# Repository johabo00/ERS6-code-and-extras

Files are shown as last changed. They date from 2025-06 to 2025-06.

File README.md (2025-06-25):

The Computer and Robot contains the files created for integration of ROS 2, running on the computer and robot respectivly
Microcontroller code is the code running on the upper ESP32 while ROS 2 is running
Hardware demo is the code running on the ESP32 without ROS 2 (described in Chapter 11)
STEPfiles contains all the custom mechanical components made for the robot.

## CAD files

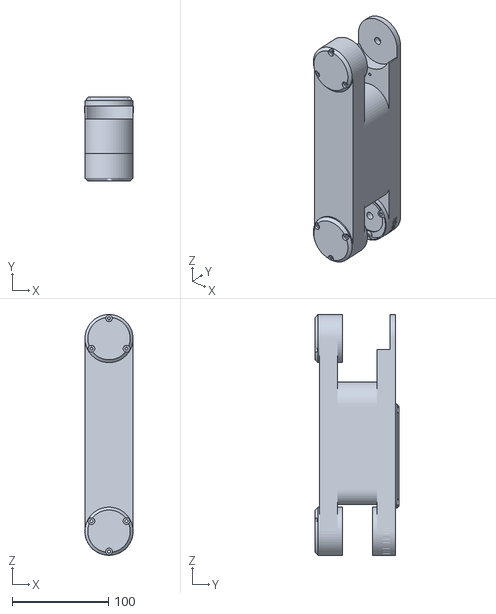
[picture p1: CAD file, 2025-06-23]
Computer/src/ers6_description/meshes/a4.stl
50.4 x 87.0 x 250.2

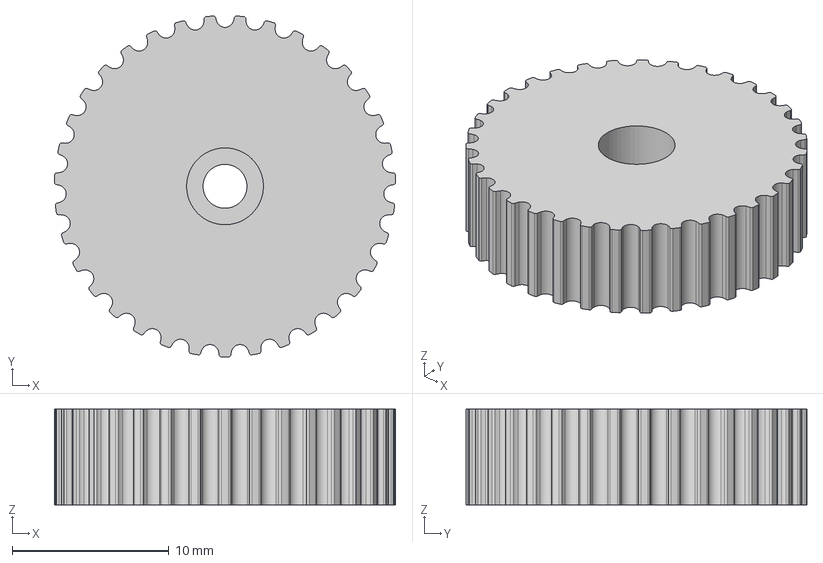
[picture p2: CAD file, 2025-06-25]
STEPfiles/P204.step
21.8 x 21.7 x 6.10 mm

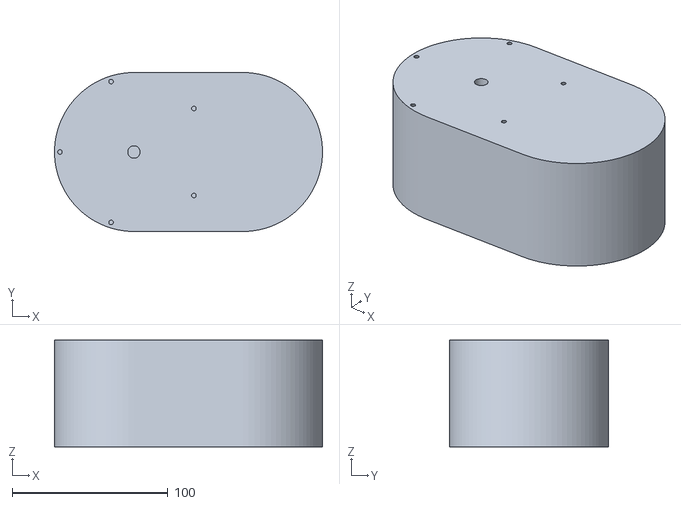
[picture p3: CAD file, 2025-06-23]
Computer/src/ers6_description/meshes/Base.stl
172.0 x 102.0 x 68.4

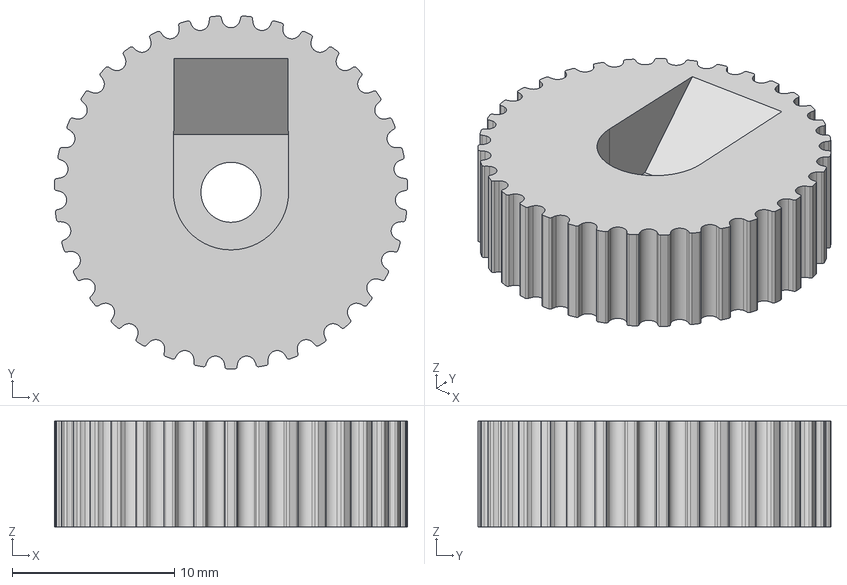
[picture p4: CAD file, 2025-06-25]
STEPfiles/P103.step
21.8 x 21.7 x 6.50 mm

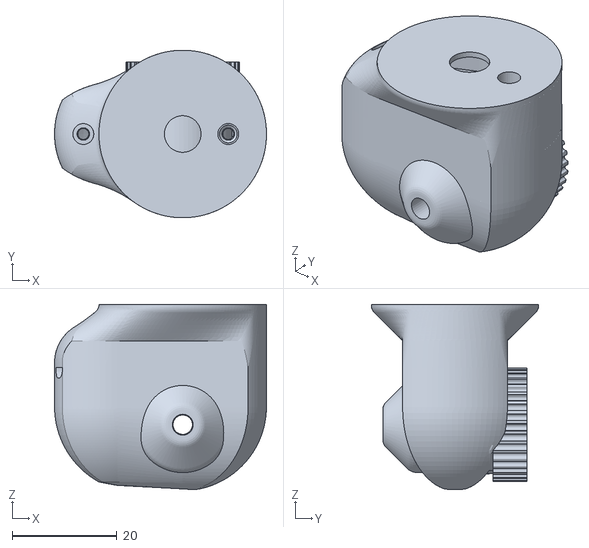
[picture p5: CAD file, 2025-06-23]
Computer/src/ers6_description/meshes/a1.stl
40.5 x 32.0 x 35.4

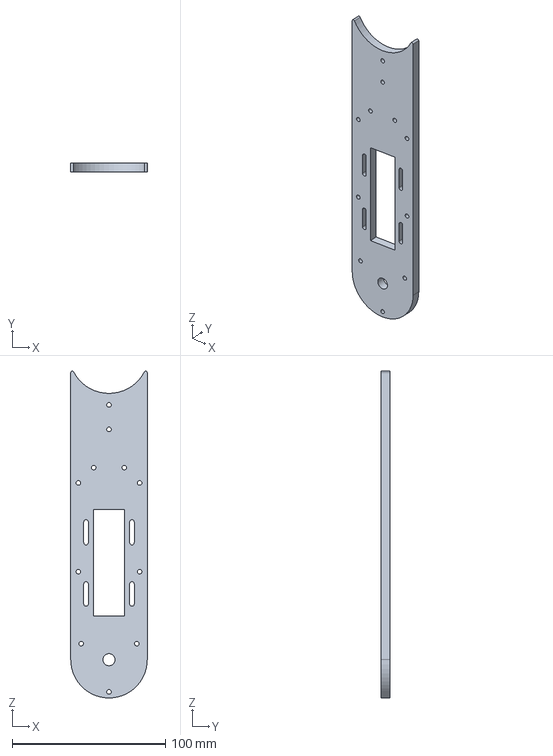
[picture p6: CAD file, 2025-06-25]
STEPfiles/W404.step
50.0 x 6.00 x 213.6 mm

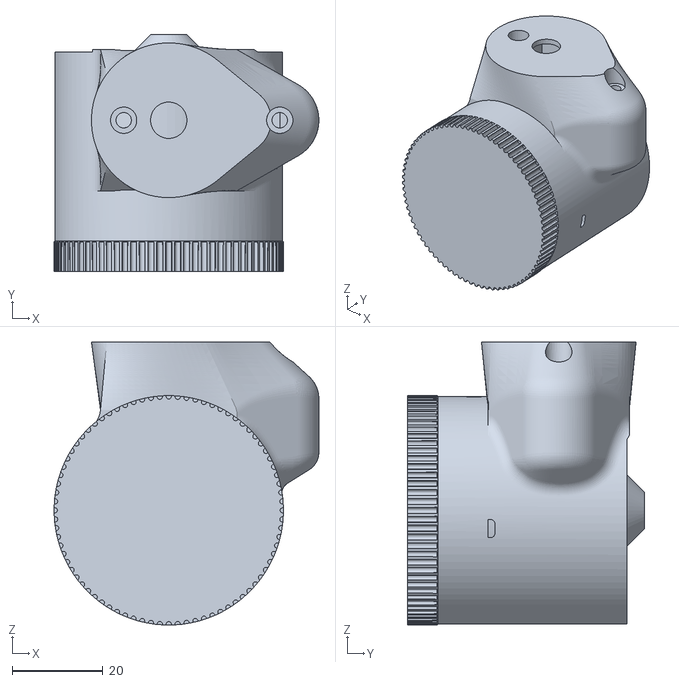
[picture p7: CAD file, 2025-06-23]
Computer/src/ers6_description/meshes/a3.stl
58.2 x 52.1 x 62.2

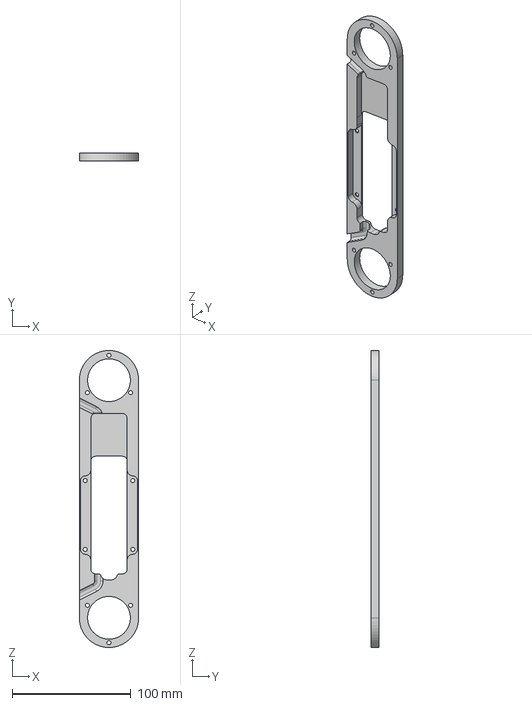
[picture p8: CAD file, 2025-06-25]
STEPfiles/P401.step
50.0 x 7.00 x 250.0 mm

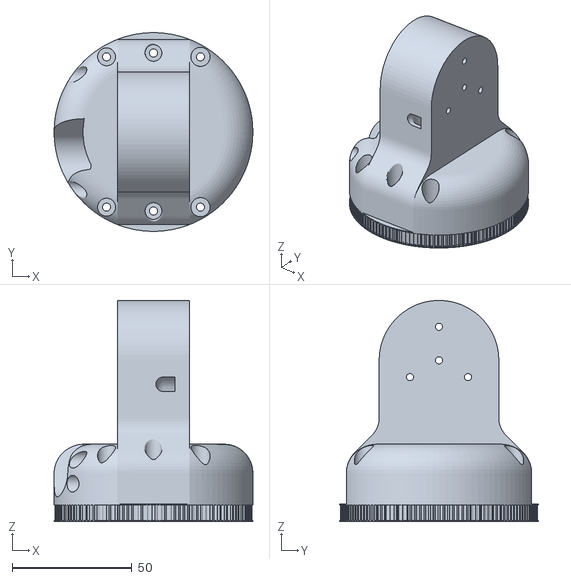
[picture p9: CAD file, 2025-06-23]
Computer/src/ers6_description/meshes/a5.stl
83.0 x 83.0 x 92.3

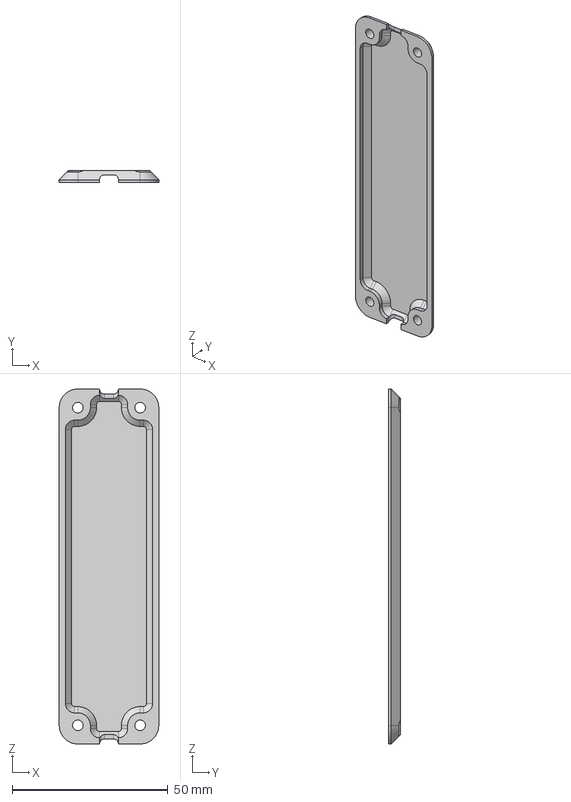
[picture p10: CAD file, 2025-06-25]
STEPfiles/P206.step
32.0 x 3.90 x 114.0 mm

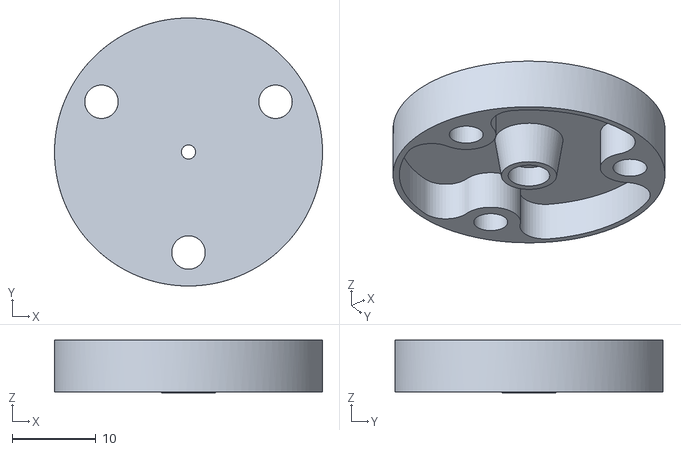
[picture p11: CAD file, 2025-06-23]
Computer/src/ers6_description/meshes/a0.stl
32.0 x 32.0 x 6.30

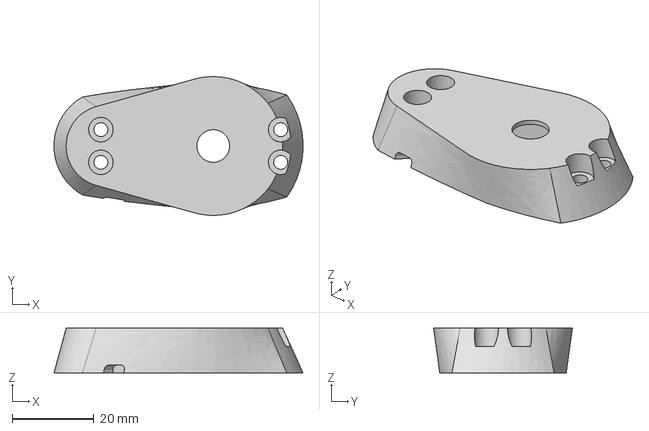
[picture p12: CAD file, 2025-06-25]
STEPfiles/P302.step
60.9 x 34.0 x 11.0 mm

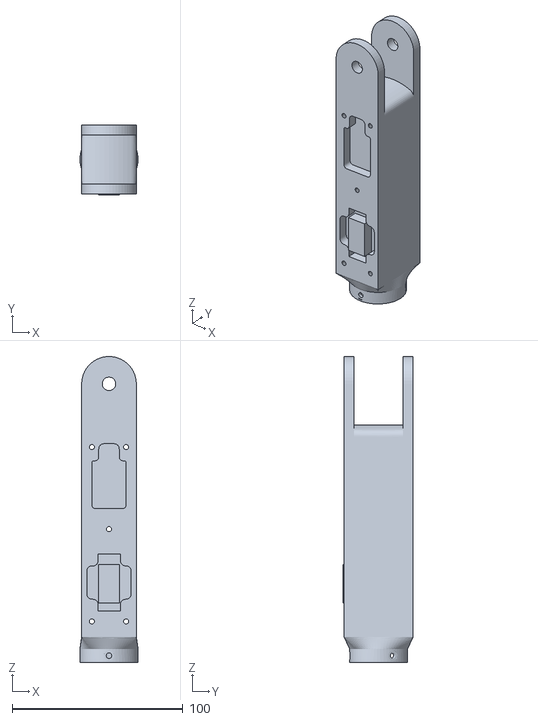
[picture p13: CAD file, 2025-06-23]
Computer/src/ers6_description/meshes/a2.stl
34.0 x 41.2 x 179.0

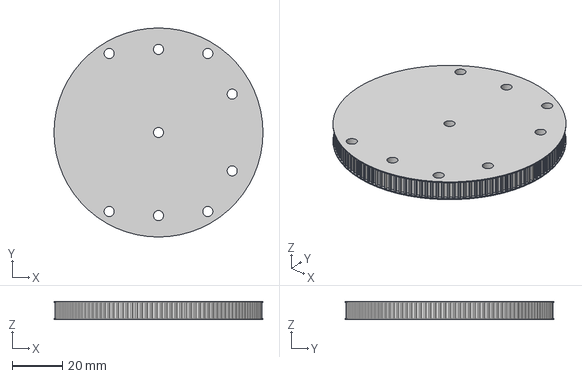
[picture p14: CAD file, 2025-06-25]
STEPfiles/P502.step
83.0 x 83.0 x 7.30 mm

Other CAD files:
STEPfiles/P102.step
STEPfiles/P205.step
STEPfiles/P506.step
STEPfiles/W603.step
STEPfiles/P101.step
STEPfiles/P104.step
STEPfiles/P201.step
STEPfiles/P202.step
STEPfiles/P203.step
STEPfiles/P301.step
STEPfiles/P303.step
STEPfiles/P304.step
STEPfiles/P402.step
STEPfiles/P403.step
STEPfiles/P404.step
STEPfiles/P405.step
STEPfiles/P406.step
STEPfiles/P407.step
STEPfiles/P408.step
STEPfiles/P409.step
STEPfiles/P410.step
STEPfiles/P411.step
STEPfiles/P501.step
STEPfiles/P503.step
STEPfiles/P504.step
STEPfiles/P507.step
STEPfiles/P601.step
STEPfiles/P602.step
STEPfiles/P603.step
STEPfiles/P606.step
STEPfiles/W201.step
STEPfiles/W202.step
STEPfiles/W401.step
STEPfiles/W402.step
STEPfiles/W403.step
STEPfiles/W501.step
STEPfiles/W502.step
STEPfiles/W601.step
STEPfiles/W602.step
STEPfiles/magholder.step

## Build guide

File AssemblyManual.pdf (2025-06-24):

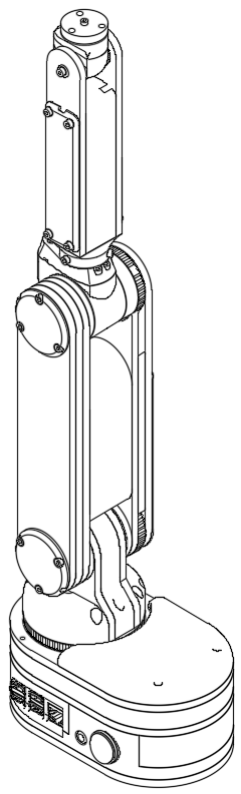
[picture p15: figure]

Assembly Manual
Version 1.0
18.06.2025

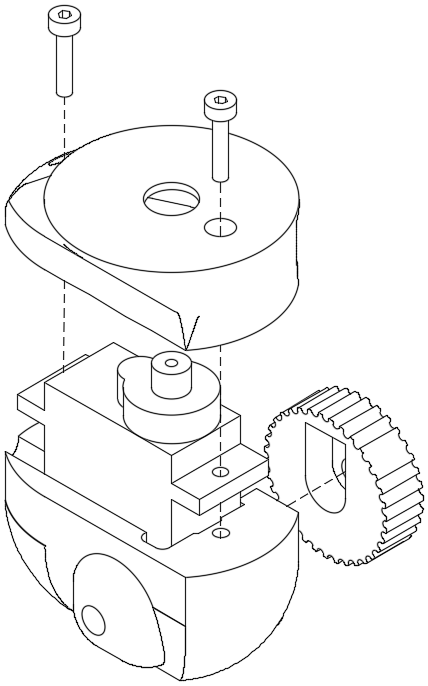
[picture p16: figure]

Assembly 1: Step 1
- Custom: P101, P102, P103
- Ordered: MG90S
- Bolts: M2x10mm [x2]
- Fasten the servo motor between P101 and P102 (screws directly into the plastic)
- Motor wires are channeled out an opening in the back P103 sits loose on P101

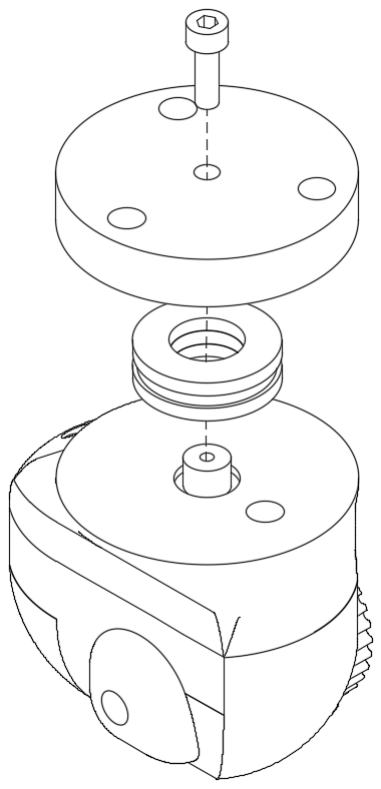
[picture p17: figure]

Assembly 1: Step 2
- Custom: P104
- Ordered: Thrust bearing (16x8x5)
- Bolts: M2.5x8mm
- Fasten P104 to the servo shaft, separated by the thrust bearing. Use thread-lock glue

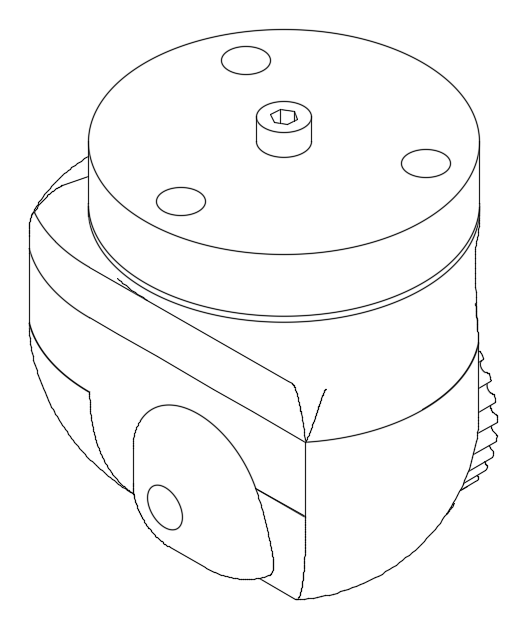
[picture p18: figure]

Assembly 2: Step 1
- Custom: P203, P204
- Ordered: MG90S
- Bolts: M2x8mm [x2], M2.5x5mm [x1]
- Fastenthe servomotor to P203 with the M2 bolts.
- Fasten P204 to the servo-shaft with a M2.5 bolt, use threadlock glue.

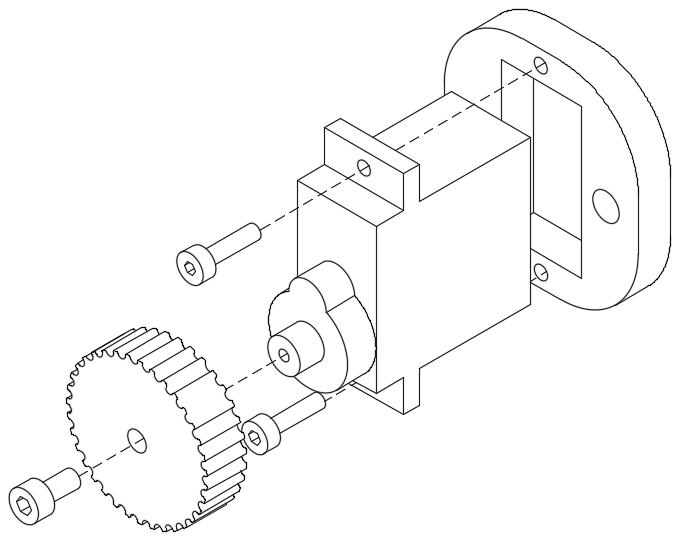
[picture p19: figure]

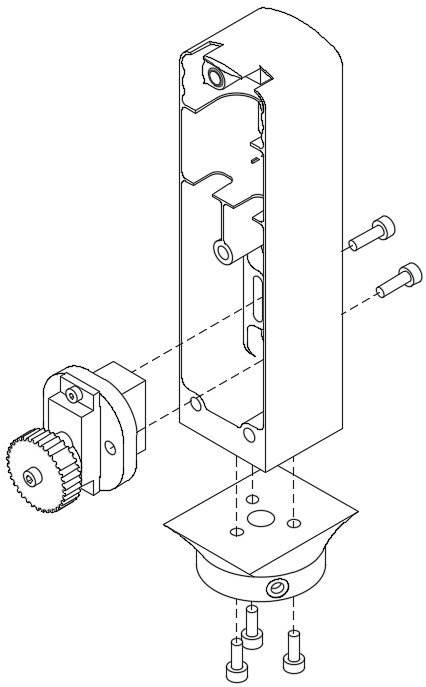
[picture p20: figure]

Assembly 2: Step 2
- Custom: P201, P202
- Bolts: M3x8mm [x3], M3x10mm [x2]
- Fasten P201 and P202 with three M3x8
- Connect the motor assembly to the slots so it can move up and down

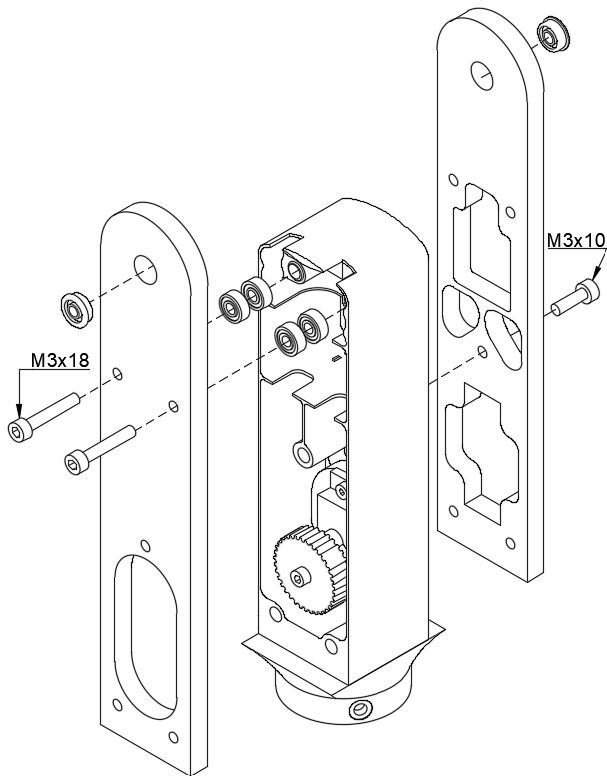
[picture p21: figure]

Assembly 2: Step 3
- Custom: W201, W202
- Ordered: MR83ZZ [x4], MF83ZZ [x2], GT2 Timing belt
- Bolts: M3x10mm [x1], M3x18mm [x2]
- Position the timing belt around P204 and between the MR83ZZ bearings
- Fasten W202 to P201 with two M3x18 bolts. NB: they go through the bearings placed above
- W201 is connected by a single M3x10
- Press the MF83ZZ into place

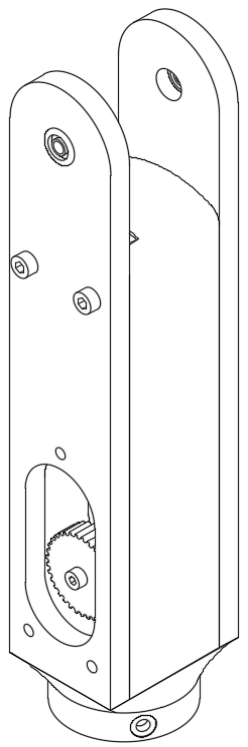
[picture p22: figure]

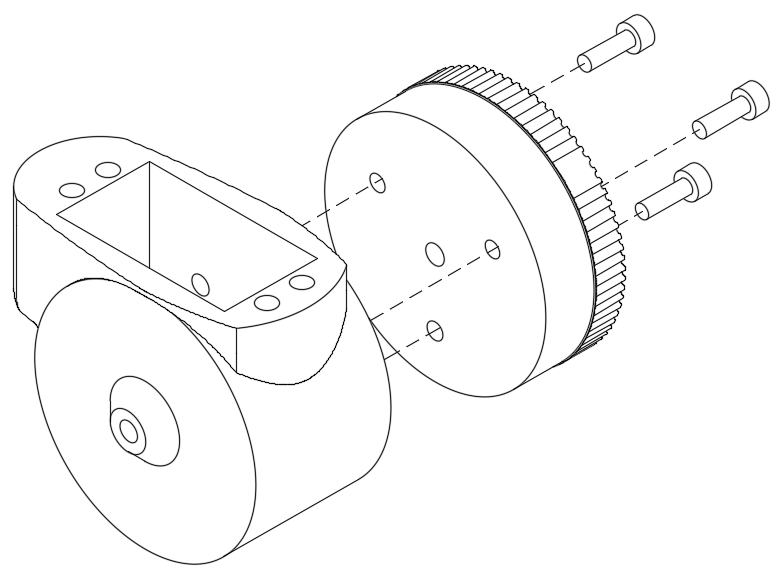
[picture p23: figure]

Assembly 3: Step 1
- Custom: P301, P303
- Bolts: M3x10 [x3]
- Connect P301 and P302 with three M3x10 bolts

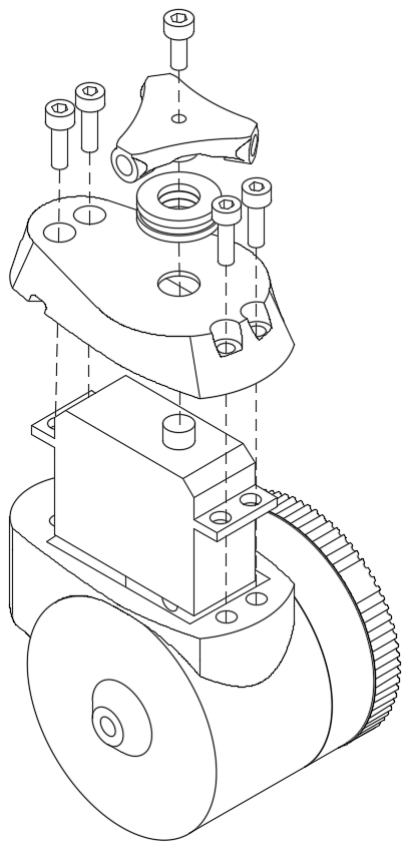
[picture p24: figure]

Assembly 3: Step 2
- Custom: P302, P304
- Ordered: TD-9225MG, Thrust bearing (16x8x5)
- Bolts: M3x8 [x1], M3x10 [x4]
- Mount the servo motor in between P301 and P302 with four M3x10 bolts. Motor cables are led out a channel in the back
- Fasten P304 to the servo shaft with a M3x8 with a thrust-bearing in between. Use threadlock glue

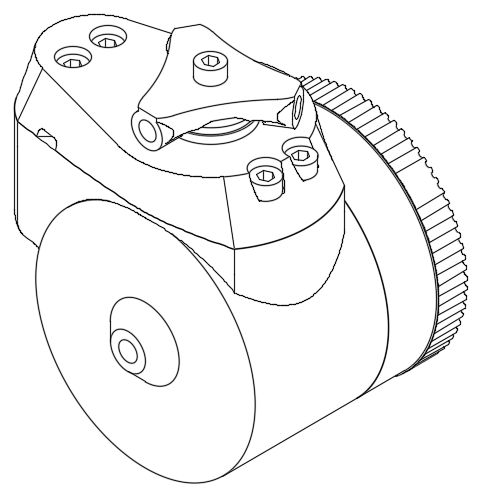
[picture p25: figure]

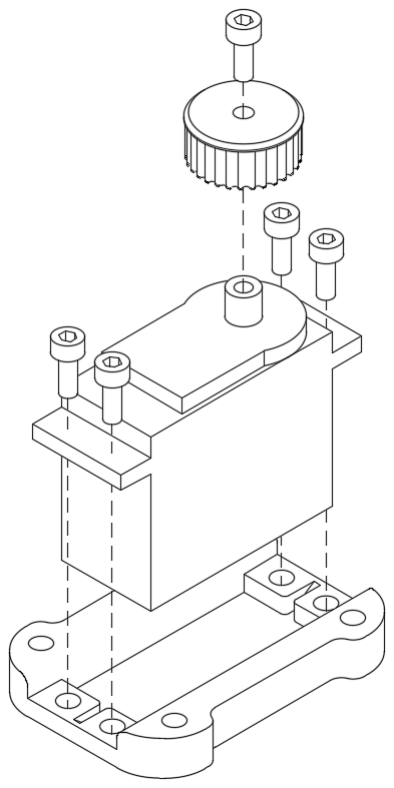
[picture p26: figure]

Assembly 4: Step 1
- Custom: P406, P410
- Ordered: MG996R
- Bolts: M3x8 [x5]
- Mount the servo motor to P406 with four bolts
- Fasten P410 to the servo shaft with a M3x8. Use threadlock glue

Assembly 4: Step 2
- Custom: P404, P407, P408, W404
- Bolts: M3x10 [x4], M3x12 [x5]

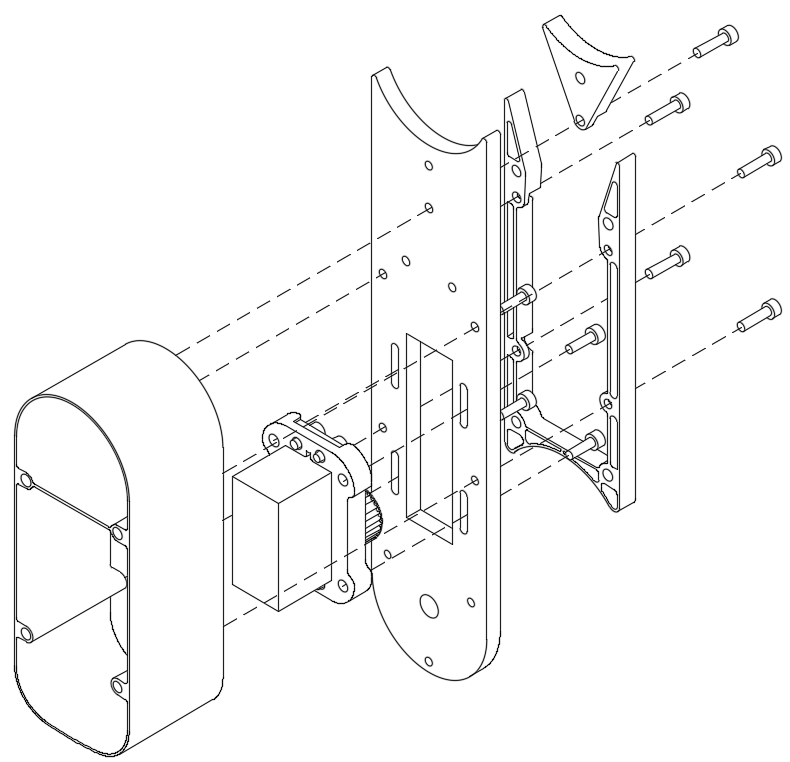
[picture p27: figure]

- Mount the motor assembly to W404
- Fasten P404, P407 and P408 with 5 M3x12

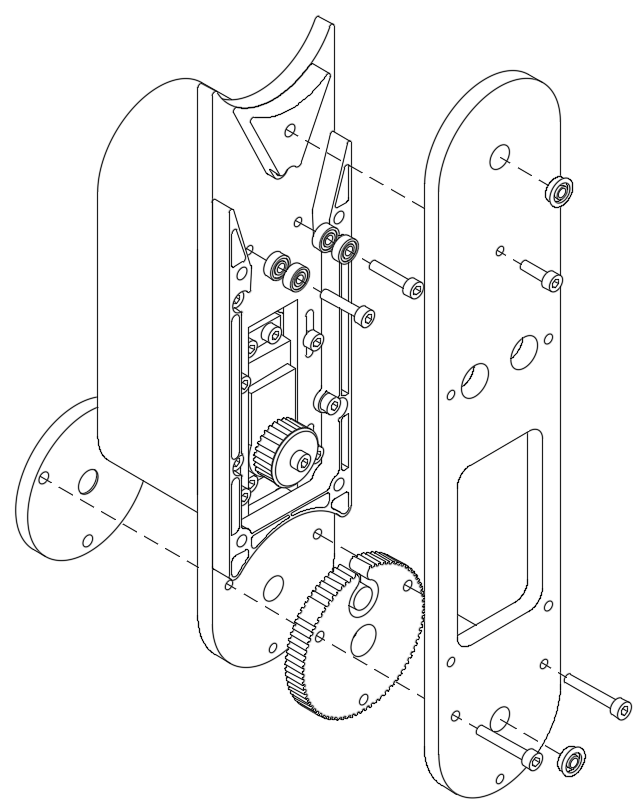
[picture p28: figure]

Assembly 4: Step 3
- Custom: P403, P409, W403
- Ordered: MR83ZZ [x4], MF83ZZ [x2], GT2 Timing belt, GT2 Timing belt
- Bolts: M3x10 [x1], M3x15 [x2], M3x22 [x2]
- Fasten the MR83ZZ with
M3x15
- Place the timing belts in position
- Fasten W403, P403 and P409. NB a ziptie can be used
around the belt in the gap
- Press in the MF83ZZ. The lower goes to W404

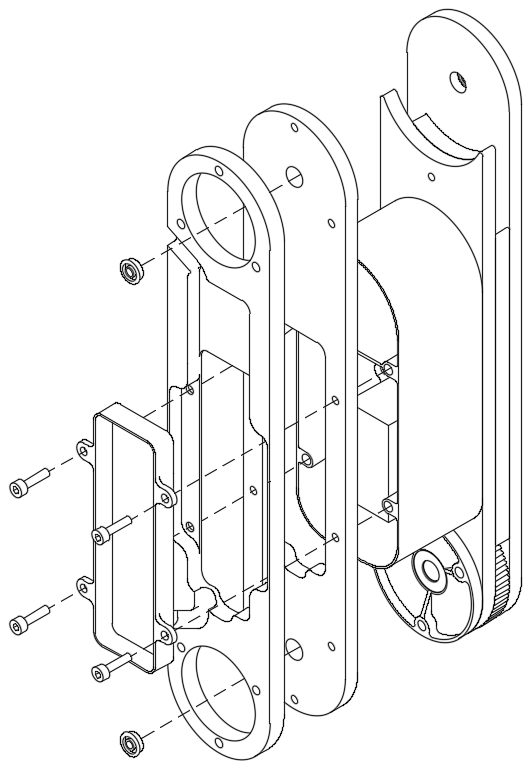
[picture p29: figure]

Assembly 4: Step 4
- Custom: P401, P402, W401
- Ordered: MF83ZZ [x2]
- Bolts: M3x12 [x4]
- Fasten P401, P402 and W401 to P404 with M3x12
- The motor cables are routed out underneeth P402
- Press in the MF83ZZ

Assembly 5: Step 1
- Custom: P501, P502, W502
- Bolts: M3x10 [x4]
- Fasten P501 and P502
- Fasten W502 to P501

Assembly 5: Step 2
- Custom: P503, P505, W501
- Ordered: MG996R
- Bolts: M3x8 [x1], M3x25 [x4]

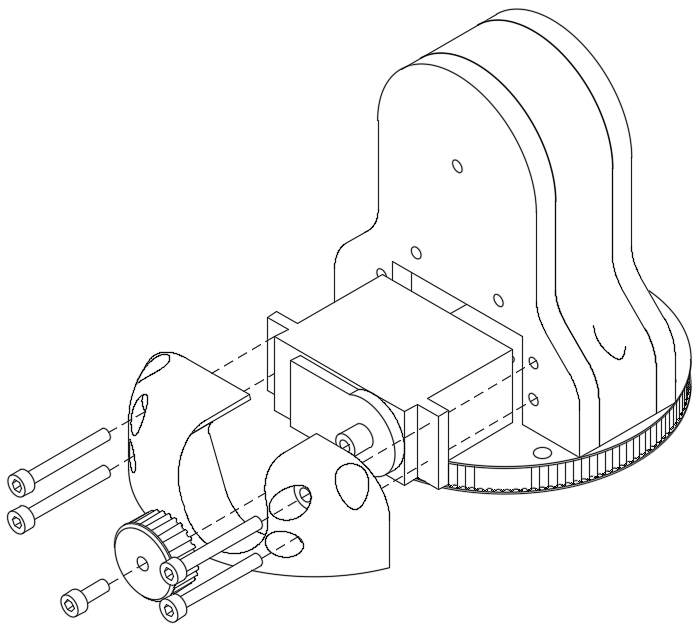
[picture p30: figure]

- Mount the servo, W501 and P503 to P501 with 4 M3x25
- Fasten P505 to the servo shaft with a M3x8, use threadlock glue

Assembly 5: Step 3
- Custom: P506, P507
- Ordered: MR83ZZ [x4]
- Bolts: M3x10 [x3], M3x15 [x1], M3x25 [x1]

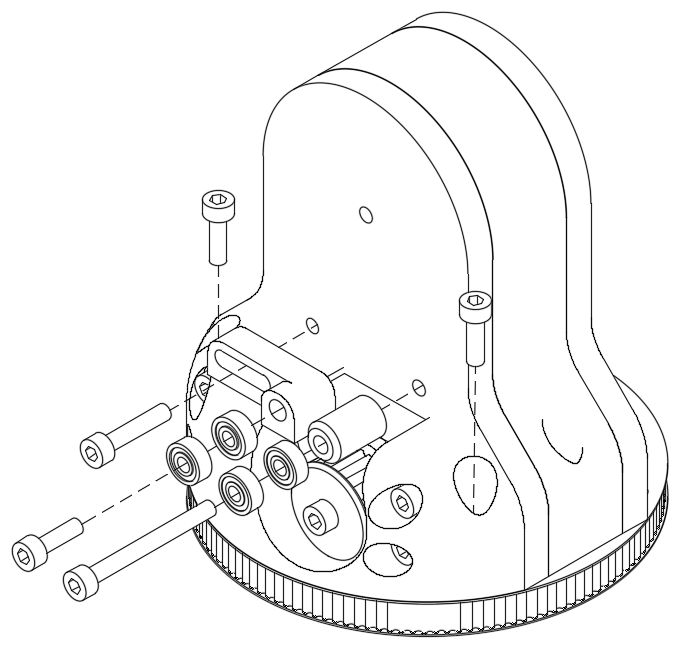
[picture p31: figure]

- Fasten P503 to P502 with two M3x10
- Mount P506 to W501/P501
with M3x15
- Fasten 2 bearings in P506 with a M3x10
- Fasten 2 bearings through P507 to P501 with a M3x25

Assembly 6: Step 1
- Custom: P601
- Ordered: DC/DC Converter, Switch, Barrel Jack, Raspberry Pi
- Press the Raspberry into position in P601
- Fit the barrel jack and switch
- Place the DC/DC converter
- Make the connections
between switch, jack and
converter

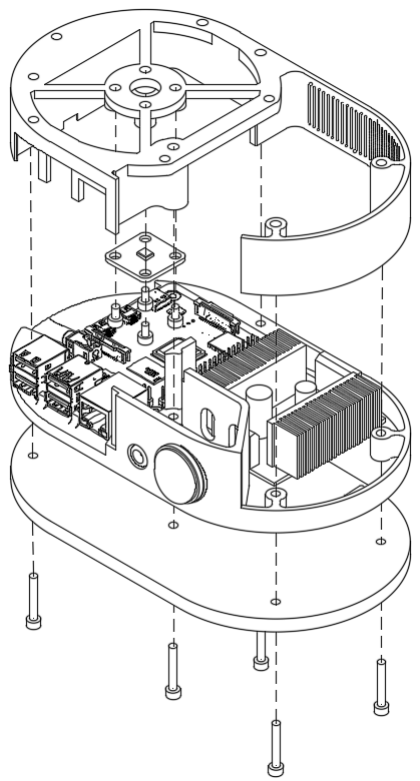
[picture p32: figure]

Assembly 6: Step 2
- Custom: P602, W601
- Ordered: AS5600
- Bolts: M3x5 [x4], M3x20 [x5]
- Fasten the AS5600 with 4 M3x5
- Fit P602 to P601
- Fasten W601 with 5 M3x20

Assembly 6: Step 3
- Custom: P604, P605, W603
- Ordered: MG996R
- Bolts: M3x8 [x5], M3x10 [x4]
- Mount the servo motor to P604 with 4 M3x8
- Fasten P605 to the servo shaft with a M3x8. Use threadlock glue
- Fasten P604 to W601 with 4 M3x10

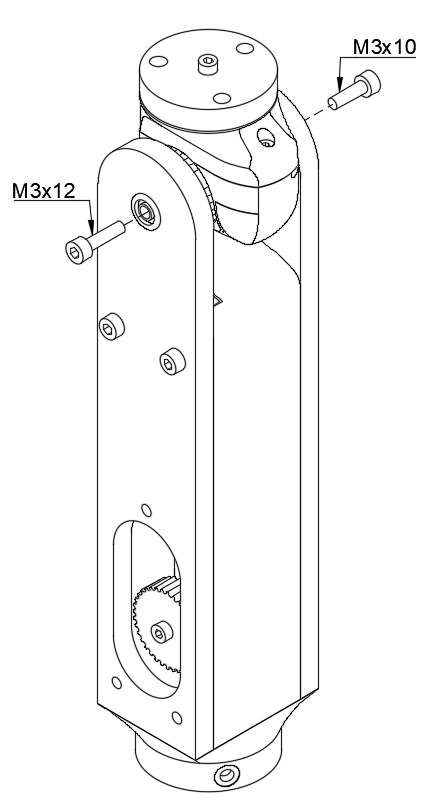
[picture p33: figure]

General assembly: Step 1
- Assemblies: A1, A2
- Bolts: M3x10 [x1], M3x12 [x1]
- Fit the A1 in A2, make sure the timing belt goes around A1 pulley
- Fasten with bolts, use
threadlock glue. NB: not tight, ensure free rotation

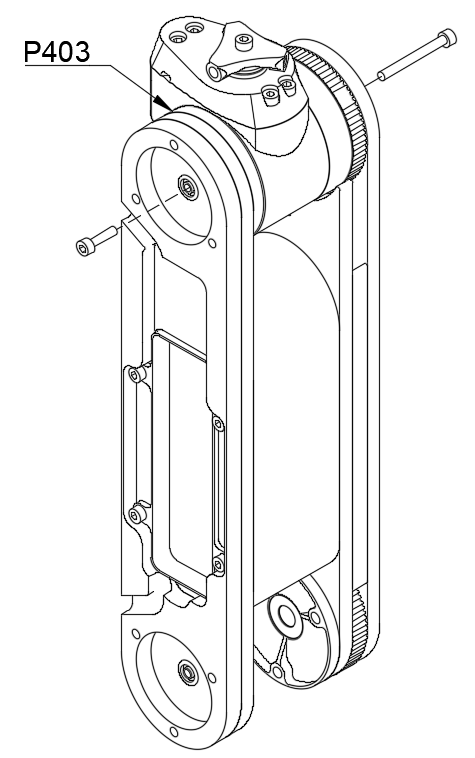
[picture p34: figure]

General assembly: Step 2
- Assemblies: A3, A4
- Components: P403
- Bolts: M3x12 [x1], M3x30 [x1], M3 standoff (5mm)
- Place P403 in position, this will be fastened later
- Fasten the M3x12 to the
standoff, through the bearing (cable side)
- Fasten A3 to the two bolts, use threadlock glue
- The belt can be tensioned

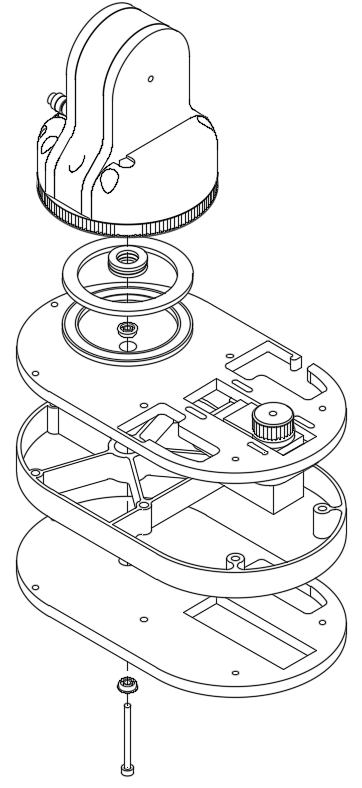
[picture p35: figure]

General assembly: Step 3
- Assemblies: A5
- Components: P603, W602,
W603, Thrust-bearing duct
- Ordered: MF83ZZ [x2], Thrust bearing(18x10x5.5), 4.5mm steel balls
- Bolts: M3x35 [x1]
- Fill the printed thrust bearing with metal balls, use
lubrication
- Press MF83ZZ to W602 and W603
- Fasten A5 to the A6 assembly with a M3x35

General assembly: Step 4
- Assemblies: A5, A6
- Components: Magnetholder
- Bolts: M3x35 [x5]
- Pressfit the magnetholder with magnet to the M3x35
connecting A5 to A6
- Connect with 5 M3x35

General assembly: Step 5
- Assemblies: A1-A4
- Bolts: M3x5 [x3]
- Connect A2 to A3 with 3 M3x5

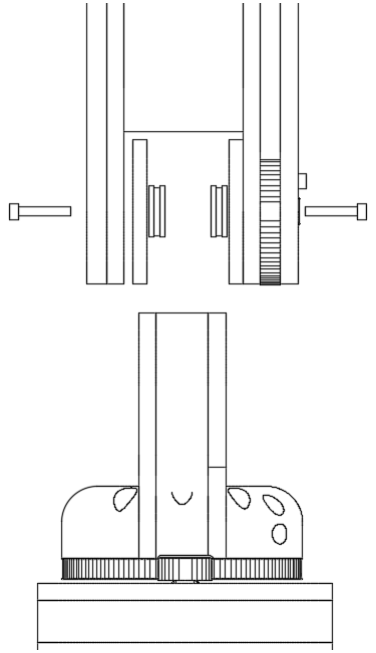
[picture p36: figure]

General assembly: Step 6
- Assemblies: All
- Components: P403
- Ordered: Thrust bearing
(18x10x5.5)
- Bolts: M3x18 [x2]
- Place P403 and bearings
- Slide onto A5 and fasten with bolts

Cabeling
- Ordered: ESP32-C3 supermini [x2], wires, I2C multiplexer
- Bolts: M3x5 [x4]
- Use the schematics figure from chapter 9
- One ESP32 is going in A2, the other in A6
- The power cables are connected in DC/DC-converter for A6, two M3x5 and inserts in A5 and A2
- I2C lines are connected with JST connectors
- I2C on AS5600 goes through the I2C multiplexer
(NB: Cables are soldered directly to board)
- It is recommended to use cable-sleeves in A6-A5, A5-A4 and A4-A3
- Set 5v output on converter
(wago-terminals can be used in A4)

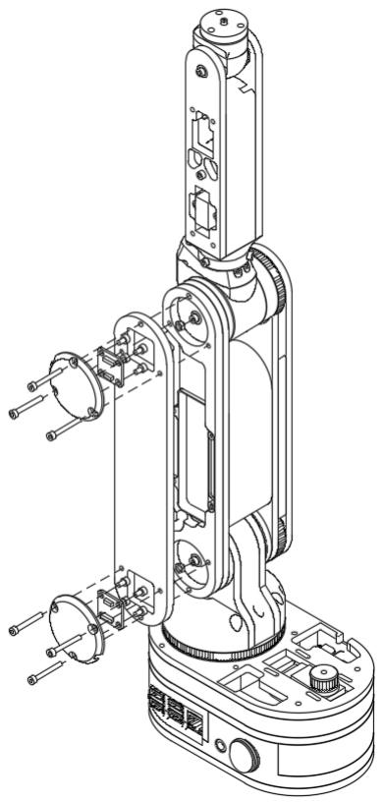
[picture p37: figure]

Cover assembly: Step 1
- Components: P405 [x2],
W402, Magnetholder [x2]
- Ordered: AS5600 [x2]
- Bolts: M3x5 [x8], M3x25 [x25]
- Fit magnetholders w. magnets to bolts in joints
- Fasten the encoders to P405 with M3x5
- Fit all wires in cable gate in A4 and place W402 over
- Fasten P405 to A4 with M3x25

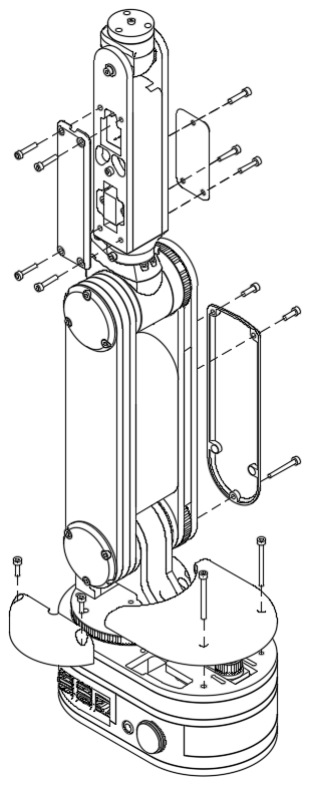
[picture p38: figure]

Cover assembly: Step 2
- Components: P205, P206,
P411, P504, P606
- Bolts: M3x10 [x4] M3x15 [x7], M3x25 [x1], M3x35 [x2]
- Fasten P205 and P206 with M3x15
- Fasten P411 with 2 M3x10 and 1 M3x25
- Fasten P504 with 2 M3x10
- Fasten P606 with 2 M3x35

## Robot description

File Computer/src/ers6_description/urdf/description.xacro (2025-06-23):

<?xml version="1.0"?>
<robot name="ers6" xmlns:xacro="http://ros.org/wiki/xacro">

  <!-- Optional properties for mesh scale and material reuse -->
  <xacro:property name="mesh_scale" value="0.001 0.001 0.001"/>

  <!-- Include modular link/joint definitions (could be broken into multiple files later) -->

  <link name="world" />

  <joint name="world_to_base_link" type="fixed">
    <parent link="world" />
    <child link="base_link" />
    <origin xyz="0 0 0" rpy="0 0 0" />
  </joint>

  <!-- === base_link === -->
  <xacro:macro name="link_with_mesh" params="link_name mesh_file origin_xyz origin_rpy color_rgba">
    <link name="${link_name}">
      <visual>
        <origin xyz="${origin_xyz}" rpy="${origin_rpy}" />
        <geometry>
          <mesh filename="${mesh_file}" scale="${mesh_scale}" />
        </geometry>
        <material name="${link_name}-material">
          <color rgba="${color_rgba}" />
        </material>
      </visual>
      <collision>
        <origin xyz="${origin_xyz}" rpy="${origin_rpy}" />
        <geometry>
          <mesh filename="${mesh_file}" scale="${mesh_scale}" />
        </geometry>
      </collision>
      <inertial>
        <origin xyz="${origin_xyz}" rpy="${origin_rpy}" />
        <mass value="1" />
        <inertia ixx="0.4" ixy="0" ixz="0" iyy="0.4" iyz="0" izz="0.4" />
      </inertial>
    </link>
  </xacro:macro>

  <xacro:link_with_mesh link_name="base_link" mesh_file="package://ers6_description/meshes/Base.stl" origin_xyz="0 0 0" origin_rpy="0 0 0" color_rgba="0.0762 0.0003 0.3613 1"/>

  <joint name="base_link_to_a5" type="revolute">
    <parent link="base_link" />
    <child link="a5" />
    <origin xyz="0.0 0.0005 0.0732" rpy="0 0 0" />
    <axis xyz="0 0 1"/>
    <limit effort="1000.0" lower="-1" upper="1" velocity="0.5"/>
  </joint>

  <xacro:link_with_mesh link_name="a5" mesh_file="package://ers6_description/meshes/a5.stl" origin_xyz="0.0002 0.0 -0.0037" origin_rpy="0 0 0" color_rgba="0.2232 0.1441 1 1"/>

  <joint name="a5_to_a4" type="revolute">
    <parent link="a5" />
    <child link="a4" />
    <origin xyz="0.1692 0.0 0.0620" rpy="0 0 1.5708" />
    <axis xyz="0.0 -1.0 -0.0018"/>
    <limit effort="1000.0" lower="-1" upper="1" velocity="0.5"/>
  </joint>

  <xacro:link_with_mesh link_name="a4" mesh_file="package://ers6_description/meshes/a4.stl" origin_xyz="0 0 0" origin_rpy="0 0 0" color_rgba="0.3564 0.6583 0.0742 1"/>

  <joint name="a4_to_a3" type="revolute">
    <parent link="a4" />
    <child link="a3" />
    <origin xyz="0 0.1685 0.20" rpy="0 0 3.141592653589793" />
    <axis xyz="0.0 -1.0 0.0032"/>
    <limit effort="1000.0" lower="-1" upper="1" velocity="0.5"/>
  </joint>

  <xacro:link_with_mesh link_name="a3" mesh_file="package://ers6_description/meshes/a3.stl" origin_xyz="0.0 0.0 0.0372" origin_rpy="0 0 0" color_rgba="0.855 0.04971 0.0497 1"/>

  <joint name="a3_to_a2" type="revolute">
    <parent link="a3" />
    <child link="a2" />
    <origin xyz="0.0005 -0.0006 0.0331" rpy="0 0 0" />
    <axis xyz="0 0 1"/>
    <limit effort="1000.0" lower="-1" upper="1" velocity="0.5"/>
  </joint>

  <xacro:link_with_mesh link_name="a2" mesh_file="package://ers6_description/meshes/a2.stl" origin_xyz="-0.0159 -0.03442 0" origin_rpy="0 0 0" color_rgba="0.6376 0.6724 0.8796 1"/>

  <joint name="a2_to_a1" type="revolute">
    <parent link="a2" />
    <child link="a1" />
    <origin xyz="-0.0004 0.0001 0.1682" rpy="0 0 3.141592653589793" />
    <axis xyz="0.0 1.0 0.0041"/>
    <limit effort="1000.0" lower="-1" upper="1" velocity="0.5"/>
  </joint>

  <xacro:link_with_mesh link_name="a1" mesh_file="package://ers6_description/meshes/a1.stl" origin_xyz="-0.0004 -0.0005 0.0243" origin_rpy="0 0 0" color_rgba="0.1981 0.4287 0.0152 1"/>

  <joint name="a1_to_a0" type="revolute">
    <parent link="a1" />
    <child link="a0" />
    <origin xyz="0.0 -0.0004 0.0279" rpy="0 0 -1.5707963267948961" />
    <axis xyz="0 0 1"/>
    <limit effort="1000.0" lower="-1" upper="1" velocity="0.5"/>
  </joint>

  <xacro:link_with_mesh link_name="a0" mesh_file="package://ers6_description/meshes/a0.stl" origin_xyz="0 0 0" origin_rpy="0 0 0" color_rgba="0.3095 0.0015 0.3515 1"/>

</robot>

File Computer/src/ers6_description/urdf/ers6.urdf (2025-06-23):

<robot name="ers6">
  <link name="world"></link>
  <joint name="base_joint" type="fixed">
    <parent link="world" />
    <child link="base_link" />
    <origin xyz="0 0 0" rpy="0 0 0" />
  </joint>
  <link name="base_link">
    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
    <inertial>
      <origin xyz="0 0 0" rpy="0 0 0" />
      <mass value="1" />
      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
    </inertial>
  </link>
  <joint name="base_link_to_a5" type="revolute">
    <parent link="base_link" />
    <child link="a5" />
    <origin xyz="0.000060582689466064966 0.0004769508252860928 0.0732228209466252" rpy="0 0 0" />
    <axis xyz="0 0 1"/>
    <limit effort="1000.0" lower="-1" upper="1" velocity="0.5"/>  </joint>
  <link name="a5">
    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
    <inertial>
      <origin xyz="0.00024149299047160257 -0.00006662961777630398 -0.003721416044104253" rpy="0 0 0" />
      <mass value="1" />
      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
    </inertial>
  </link>
  <joint name="a5_to_a4" type="revolute">
    <parent link="a5" />
    <child link="a4" />
    <origin xyz="0.16917411790950931 0.00002629570427786776 0.06198128719208244" rpy="0 0 1.5707963267948963" />
    <axis xyz="2.2204424853991772e-16 -0.9999983949841352 -0.001791655422669125"/>
    <limit effort="1000.0" lower="-1" upper="1" velocity="0.5"/>  </joint>
  <link name="a4">
    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
    <inertial>
      <origin xyz="0 0 0" rpy="0 0 0" />
      <mass value="1" />
      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
    </inertial>
  </link>
  <joint name="a4_to_a3" type="revolute">
    <parent link="a4" />
    <child link="a3" />
    <origin xyz="0 0.1685 0.20" rpy="0 0 3.141592653589793" />
    <axis xyz="2.2204349637747346e-16 -0.9999950075456312 0.0031598866772435397"/>
    <limit effort="1000.0" lower="-1" upper="1" velocity="0.5"/>  </joint>
  <link name="a3">
    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
    <inertial>
      <origin xyz="7.399065680067473e-20 0 0.0371754409751881" rpy="0 0 0" />
      <mass value="1" />
      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
    </inertial>
  </link>
  <joint name="a3_to_a2" type="revolute">
    <parent link="a3" />
    <child link="a2" />
    <origin xyz="0.0005014862197909482 -0.0005754625084648142 0.03310193380359011" rpy="0 0 0" />
    <axis xyz="0 0 1"/>
    <limit effort="1000.0" lower="-1" upper="1" velocity="0.5"/>  </joint>
  <link name="a2">
    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
    <inertial>
      <origin xyz="-0.015941182779098312 -0.03442337337371612 0" rpy="0 0 0" />
      <mass value="1" />
      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
    </inertial>
  </link>
  <joint name="a2_to_a1" type="revolute">
    <parent link="a2" />
    <child link="a1" />
    <origin xyz="-0.0004211425734971276 0.00007487255719667088 0.16818515224205283" rpy="0 0 3.141592653589793" />
    <axis xyz="-4.4408551769028203e-16 0.999991685995294 0.004077737153082017"/>
    <limit effort="1000.0" lower="-1" upper="1" velocity="0.5"/>  </joint>
  <link name="a1">
    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
    <inertial>
      <origin xyz="-0.00042114257349712755 -0.0005282776510994319 0.024270987241524544" rpy="0 0 0" />
      <mass value="1" />
      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
    </inertial>
  </link>
  <joint name="a1_to_a0" type="revolute">
    <parent link="a1" />
    <child link="a0" />
    <origin xyz="1.6263032587282567e-19 -0.0003501459947950203 0.02786555015025216" rpy="0 0 -1.5707963267948961" />
    <axis xyz="0 0 1"/>
    <limit effort="1000.0" lower="-1" upper="1" velocity="0.5"/>  </joint>
  <link name="a0">
    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
    <inertial>
      <origin xyz="0 0 0" rpy="0 0 0" />
      <mass value="1" />
      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
    </inertial>
  </link>

</robot>

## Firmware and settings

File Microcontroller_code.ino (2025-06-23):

#include "Wire.h"
#include <ESP32Servo.h>

#define I2C_ADDR 0x20
#define NUM_SERVOS 3

#define SERVO0_PIN 2
#define SERVO1_PIN 4
#define SERVO2_PIN 5

Servo servo0;
Servo servo1;
Servo servo2;

int current_angles[NUM_SERVOS] = {90, 90, 90};
int angle_targets[NUM_SERVOS] = {90, 90, 90};
bool update_flags[NUM_SERVOS] = {false, false, false};

void receiveEvent(int len) {
  while (Wire.available() >= 3) {
    uint8_t channel = Wire.read();
    uint8_t high = Wire.read();
    uint8_t low = Wire.read();

    if (channel < NUM_SERVOS) {
      int16_t value = (high << 8) | low; // -1000 to +1000
      int angle = map(value, -1000, 1000, 0, 180);
      angle = constrain(angle, 0, 180);

      angle_targets[channel] = angle;
      update_flags[channel] = true;
    }
  }
}

void requestEvent() {
  for (int i = 0; i < NUM_SERVOS; ++i) {
    int16_t pos = current_angles[i];
    Wire.write((uint8_t)(pos >> 8));
    Wire.write((uint8_t)(pos & 0xFF));
  }
}

void moveServo(Servo& servo, int index) {
  if (update_flags[index]) {
    update_flags[index] = false;
    int angle = angle_targets[index];
    servo.write(angle);
    current_angles[index] = angle;
  }
}

void setup() {
  // Attach servos
  servo0.attach(SERVO0_PIN);
  servo1.attach(SERVO1_PIN);
  servo2.attach(SERVO2_PIN);

  // Move to initial positions
  servo0.write(current_angles[0]);
  servo1.write(current_angles[1]);
  servo2.write(current_angles[2]);

  // Start I2C and register callbacks
  Wire.begin((uint8_t)I2C_ADDR);
  Wire.onReceive(receiveEvent);
  Wire.onRequest(requestEvent);
}

void loop() {
  moveServo(servo0, 0);
  moveServo(servo1, 1);
  moveServo(servo2, 2);
}

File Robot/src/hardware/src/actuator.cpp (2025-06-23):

#include "hardware/actuator.hpp"

Actuator::Actuator(const std::string &name, uint8_t encoder_addr, uint8_t esp32_addr,
                   uint8_t esp32_channel, bool uses_external_encoder, int mux_channel)
  : name_(name), encoder_addr_(encoder_addr), esp32_addr_(esp32_addr),
    esp32_channel_(esp32_channel), has_external_encoder_(uses_external_encoder),
    mux_channel_(mux_channel) {}

const std::string & Actuator::get_name() const { return name_; }
uint8_t Actuator::get_encoder_address() const { return encoder_addr_; }
uint8_t Actuator::get_esp32_address() const { return esp32_addr_; }
uint8_t Actuator::get_esp32_channel() const { return esp32_channel_; }
bool Actuator::uses_external_encoder() const { return has_external_encoder_; }
bool Actuator::uses_mux() const { return mux_channel_ >= 0; }
int Actuator::get_mux_channel() const { return mux_channel_; }

void Actuator::set_position(double pos) { position_ = pos; }
void Actuator::set_command(double cmd) { command_ = cmd; }
double Actuator::get_command() const { return command_; }
double Actuator::get_position() const { return position_; }

std::vector<uint8_t> Actuator::encode_command() const
{
  int16_t scaled = static_cast<int16_t>(command_ * 1000);  // Convert to fixed-point
  return { esp32_channel_, static_cast<uint8_t>(scaled >> 8), static_cast<uint8_t>(scaled & 0xFF) };
}

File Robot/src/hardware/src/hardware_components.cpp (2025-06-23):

#include "hardware/hardware_components.hpp"
#include <iostream>

// ======================= Esp32Interface =======================
Esp32Interface::Esp32Interface(const std::string &id, int i2c_address)
    : id_(id), i2c_address_(i2c_address)
{
    is_connected_ = false;
}

bool Esp32Interface::connect()
{
    std::cout << "[Esp32Interface] Connecting to ESP32 at I2C address " << i2c_address_ << "\n";
    is_connected_ = true;
    return true;
}

void Esp32Interface::disconnect()
{
    std::cout << "[Esp32Interface] Disconnected\n";
    is_connected_ = false;
}

bool Esp32Interface::read_positions(std::vector<int> &encoder_values)
{
    if (!is_connected_) return false;

    // Simulate 3 encoder values
    encoder_values = {100, 200, 300};  // Replace with actual I2C reads
    return true;
}

bool Esp32Interface::send_motor_commands(const std::vector<double> &commands)
{
    if (!is_connected_) return false;

    std::cout << "[Esp32Interface] Sending commands: ";
    for (double cmd : commands)
        std::cout << cmd << " ";
    std::cout << "\n";

    // TODO: Implement actual I2C transmission
    return true;
}

// ======================= AS5600Interface =======================

AS5600Interface::AS5600Interface(const std::string &id, int i2c_address)
    : id_(id), i2c_address_(i2c_address)
{
    is_connected_ = false;
}

bool AS5600Interface::connect()
{
    std::cout << "[AS5600Interface] Connected to AS5600 at I2C address " << i2c_address_ << "\n";
    is_connected_ = true;
    return true;
}

void AS5600Interface::disconnect()
{
    std::cout << "[AS5600Interface] Disconnected\n";
    is_connected_ = false;
}

bool AS5600Interface::read_positions(int &encoder_values)
{
    if (!is_connected_) return false;

    // Simulate a single encoder value
    encoder_values = 400;  // Replace with real I2C read from AS5600
    return true;
}
